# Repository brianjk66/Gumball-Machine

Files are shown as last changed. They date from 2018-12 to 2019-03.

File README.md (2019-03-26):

# Gumball Drink Machine
By Brian Kaplan & Adam Elghor

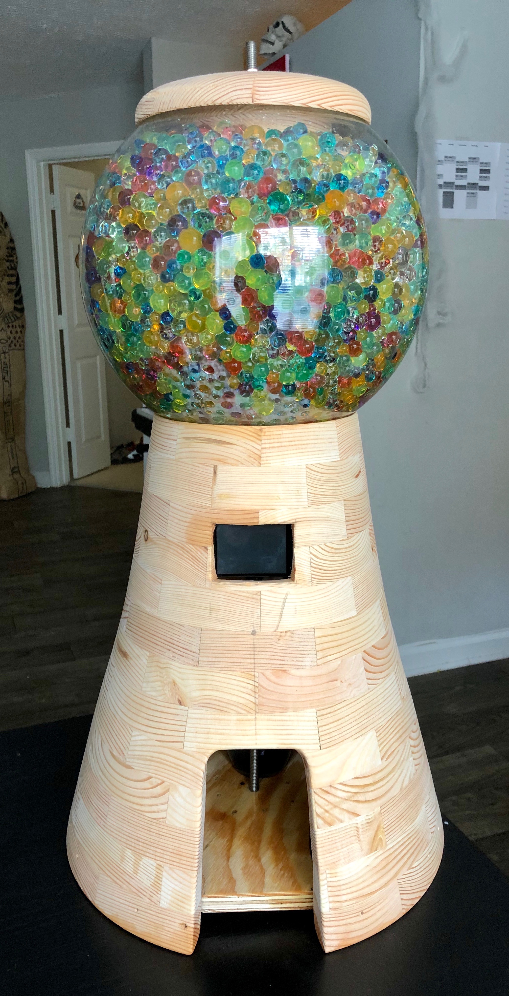
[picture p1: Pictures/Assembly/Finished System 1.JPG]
Finished System


[Project Demo](https://youtu.be/TyXLxnWFjBc)

## Project Idea
The idea of this project was to create an automated drink dispensing system centered around the mbed platform.  This project is intended to be an interactive system that mixes and dispenses internally stored drinks.  We wanted the system to resemble a gumball machine to give it a nice aesthetic and charm.

We decided to make the system gravity-fed for the sake of simplicity with the drinks being stored in a sphere at the top.  The drinks would then be dispensed via solenoid control valves into a cup at the base of the system.  The user interface to the system would be a [TFT LCD touchscreen](https://www.adafruit.com/product/2090) that a user can use to select the drink of their choice.

We also considered the use of [peristaltic pumps](https://www.adafruit.com/product/1150) for better liquid dispensing, a [liquid flow meter](https://www.adafruit.com/product/828) for better liquid measurement, and a [rotary encoder](https://www.adafruit.com/product/377) as an alternate user interface.  However, peristaltic pumps are costly (~$25 each), the flow meter was incredibly bulky and could not fit within the system, and the rotary encoder made for a confusing hybrid UI so we removed it as well.

## Hardware Setup

### Mechanical Components
The mechanical system consists of the following components:
- Handmade wooden body and lid
- 1ft Acrylic Sphere
- Assorted Color Water Beads
- 3ft Threaded Steel Dowel
- 2x Hex Nuts
- 2x Washers
- 4x Condiment Bottles
- 4x 12V Solenoid Valves (food-safe)
- Assorted Push-Fit Connecters and Fittings
- 10ft, 1/4" OD Polyethylene Tubing (food-safe)

### Electrical Components
The electrical system consists of the following components:
- Custom Printed Circuit Board:
  - mbed Microcontroller
  - 5V Linear Voltage Regulator
  - 3.3uF Ceramic Capacitor
  - 1.0uF Ceramic Capacitor
  - 4x 100 Ohm 1/4W Resistors
  - 4x 4.7k Ohm 1/4W Resistors
  - 4x 1N4001 Diodes
  - 4x N-Channel MOSFETs
  - Assorted 0.1" Male Headers
- 2.8in TFT LCD
- Flow Meter (Removed in final design)
- Rotary Encoder (Removed in final design)
- 12V, 2A Power Supply
- Barrel Jack
- Rocker Switch

## Code Setup
This system relies on using Adafruit's TFT LCD touchscreen on the mbed.  However, all of Adafruit's accompanying libraries and software support are made exclusively for Arduino (or Arduino-compatible) products.  As a result, the first major step in the software development of this project was porting the necessary Arduino libraries to the mbed.  The first library that we ported to mbed was [Adafruit's GFX Library](https://github.com/adafruit/Adafruit-GFX-Library) to provide us with a familiar graphics API.  The second library we ported was [Adafruit's ILI9341 Library](https://github.com/adafruit/Adafruit_ILI9341) for interfacing with the LCD.  The third library we ported was [Adafruit's FT6206 Library](https://github.com/adafruit/Adafruit_FT6206_Library) for interfacing with the FT6206 capacitive touch controller on the touchscreen.

Next, we wrote several test programs for testing the functionality of our hardware.  We wrote (and also used some existing) test programs for both the Arduino (before porting the libraries to mbed) and the mbed.  The Arduino test programs included a rotary encoder test, a flow meter test, and a couple LCD tests.  The mbed test programs included a flow sensor test and several LCD tests.

The final program that runs on the system is fairly straightforward.  It features 4 digital outputs for controlling each solenoid valve via a MOSFET.  There is also a touch controller and an LCD object for touchscreen I/O.  Finally a 2D array in program memory stores the hardcoded recipes for each drink.  The rows of the array correspond to recipes and the columns correspond to the proportion of each mixer in the drink.

The main loop body initializes all the peripherals as needed and sets up an interrupt routine for when a user touches the display.  If the user has selected an on-screen button corresponding to a drink, then the system dispenses the drink according to its recipe.  The dispensing routine starts a timer and opens the appropriate valves for durations that are directly proportional to the ratios provided in the recipe. The scaling factor (called TIME_SCALAR) must be calibrated based on the flow of drinks through the system

## Instructions

### Woodwork
The wooden body of the system was made by cutting several carefully measured trapezoids out of 8ft 2x4s and arranging them into 13 octagonal rings of decreasing size.  The rings were then glued together and stacked to form a conical structure.  This was then fastened to a lathe and turned down to the final shape of the system.  Cutouts were then made for the touchscreen and the cup hole.  The lid of the system was also turned on a lathe as well.

### The Sphere
The acrylic sphere had five holes drilled in it (one for structural support and 4 for tubing) and situated on top of the system.  The condiment bottles had holes drilled in their bases and had tubing fed in through the bottom and sealed with a combination of FDA-approved silicone sealant and hot glue.  The condiment bottles were placed in the sphere with the tubing passing through the previously mentioned holes and the lid was placed on top.  The threaded steel rod was cut to about 30" and fed through the lid, sphere, and bottom faceplate to serve as a central support column for the system, secured by a nut and washer on either side.

### Plumbing
The tubing assembly of the system consisted of the 4 solenoids connecting to the condiment bottles on one side.  On the other side, the solenoids connected to a set of Y-connectors to merge the 4 tubes into one for the output nozzle.  This tubing assembly was secured to the inside of the wooden body using hot glue.

### Electrical
The electrical system consisted primarily of a PCB.  The PCB took a 12V input for power and an onboard linear regulator to step the power down to 5V for the LCD and flow meter (which was later removed).  The PCB featured 4 driver sub-circuits to allow the mbed to open and close the solenoid valves (which used 12V power) via a DigitalOut pin.  The driver sub-circuits consisted of an N-channel MOSFET, a gate drive resistor, a gate pulldown resistor, and a fly-back diode.  The PCB connected touchscreen, the driver sub-circuits, the rotary encoder (removed), and the flow meter (removed) all to the appropriate mbed ports.  The PCB and touchscreen were mounted inside the body of the system using hot glue.

## Acknowledgements
We'd like to thank the PI's of the Invention Studio for all their help on this project and for providing us access to their incredible facilities for wood-working, metal-working, soldering, and PCB manufacturing.  We'd especially like to thank Morgan Cook, the Invention Studio's Director of Operations, for his continued help and support.

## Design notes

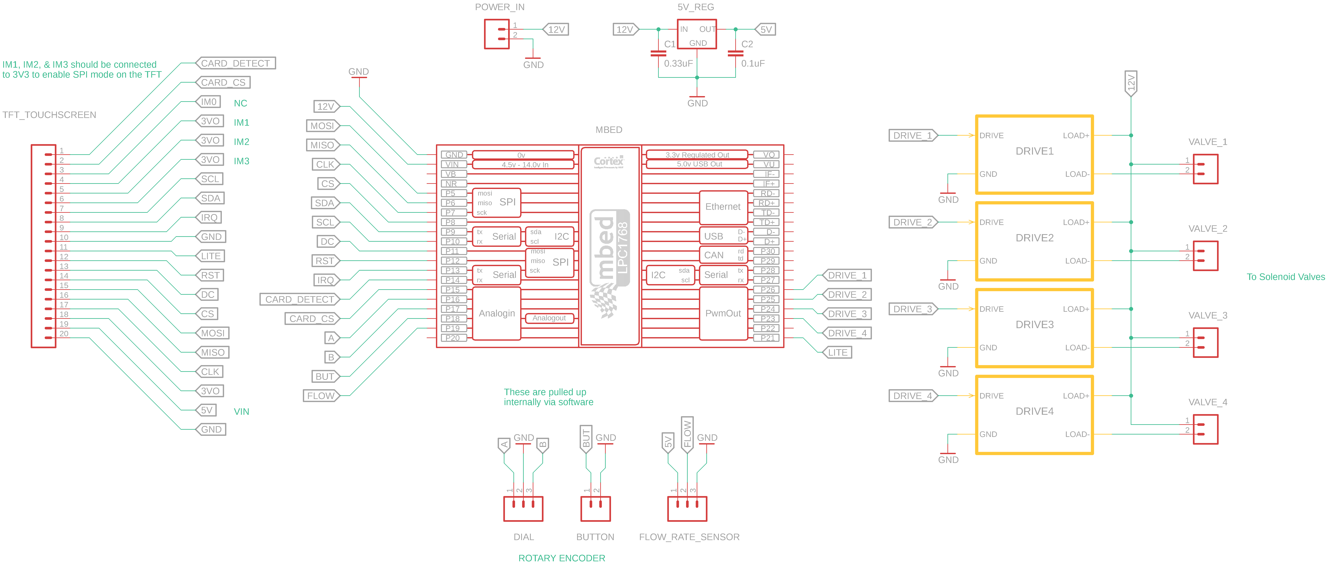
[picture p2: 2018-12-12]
Pictures/Electrical System/PCB Schematic.png

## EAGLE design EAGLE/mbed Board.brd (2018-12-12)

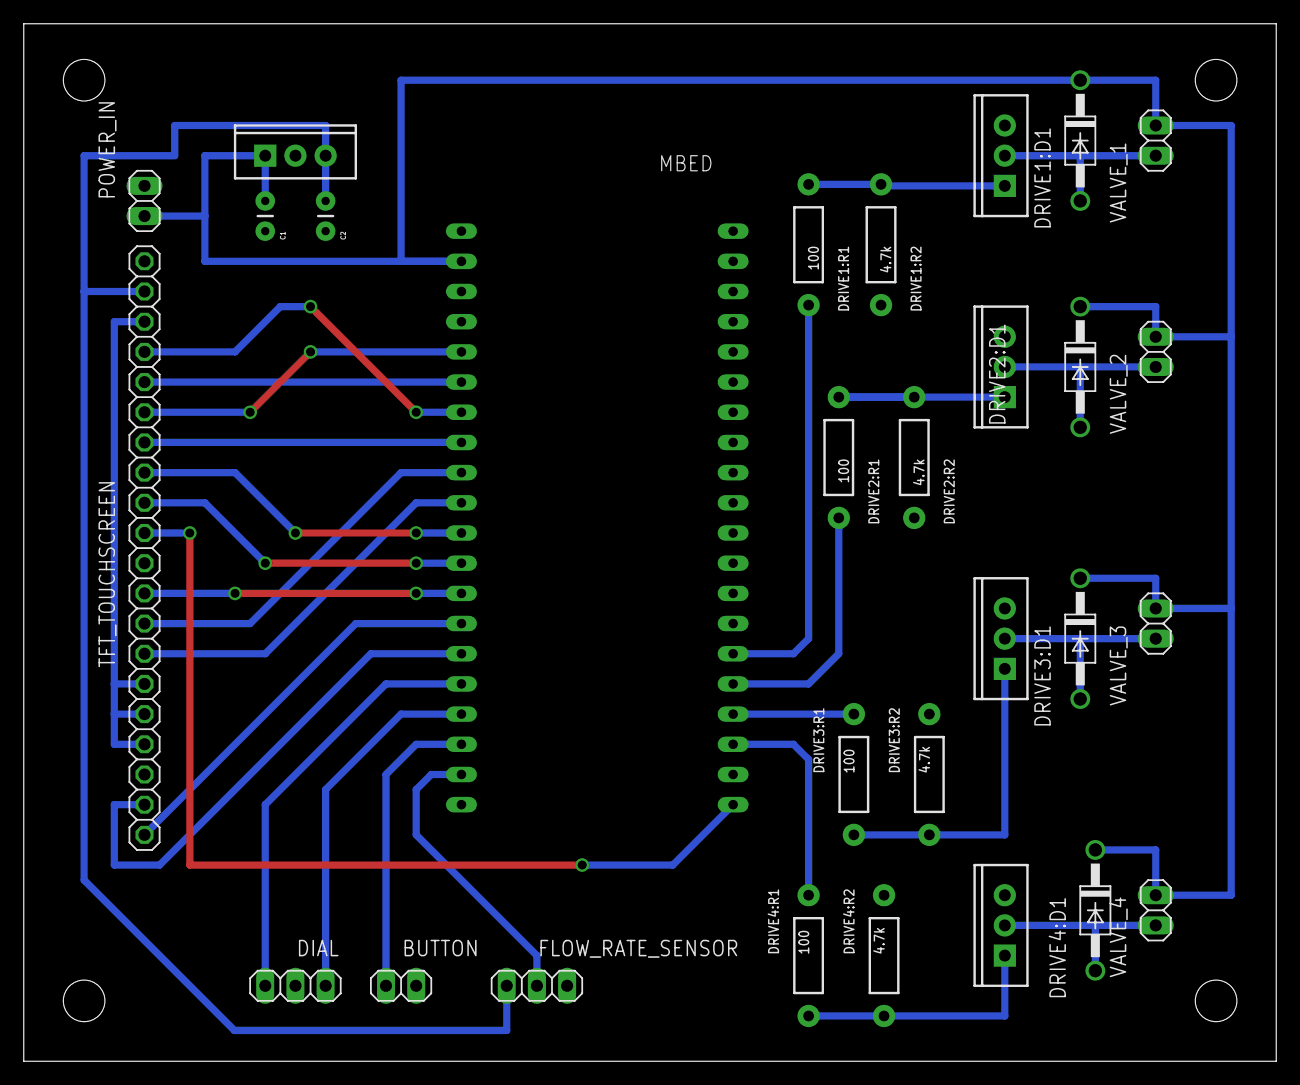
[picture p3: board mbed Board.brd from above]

Board: 2 copper layers, 105.4 x 87.3 mm, 29 parts (0 on the bottom side), 32 nets.

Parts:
5V_REG: TO-220-SINK
BUTTON: 1X02
C1: 0.33uF; CAP-PTH-SMALL
C2: 0.1uF; CAP-PTH-SMALL
DIAL: 1X03
DRIVE1:D1, DRIVE2:D1, DRIVE3:D1, DRIVE4:D1: DO-41
DRIVE1:NFET, DRIVE2:NFET, DRIVE3:NFET, DRIVE4:NFET: N-CHANNEL_MOSFETGENERIC; TO-220-SINK
DRIVE1:R1, DRIVE2:R1, DRIVE3:R1, DRIVE4:R1: 100; AXIAL-0.4
DRIVE1:R2, DRIVE2:R2, DRIVE3:R2, DRIVE4:R2: 4.7k; AXIAL-0.4
FLOW_RATE_SENSOR: 1X03
MBED: MBED_NXP_LPC1768; MBED-KIT
POWER_IN: 1X02
TFT_TOUCHSCREEN: 1X20
VALVE_1, VALVE_2, VALVE_3, VALVE_4: 1X02

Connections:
3VO: TFT_TOUCHSCREEN.4, TFT_TOUCHSCREEN.5, TFT_TOUCHSCREEN.6, TFT_TOUCHSCREEN.18
5V: 5V_REG.3, C2.1, FLOW_RATE_SENSOR.1, TFT_TOUCHSCREEN.19
12V: 5V_REG.1, C1.1, DRIVE1:D1.C, DRIVE2:D1.C, DRIVE3:D1.C, DRIVE4:D1.C, MBED.VIN, POWER_IN.1, VALVE_1.1, VALVE_2.1, VALVE_3.1, VALVE_4.1
A: DIAL.1, MBED.P$16
B: DIAL.3, MBED.P$17
BUT: BUTTON.1, MBED.P$18
CARD_CS: MBED.P$15, TFT_TOUCHSCREEN.2
CARD_DETECT: MBED.P$14, TFT_TOUCHSCREEN.1
CLK: MBED.P$7, TFT_TOUCHSCREEN.17
CS: MBED.P$8, TFT_TOUCHSCREEN.14
DC: MBED.P$11, TFT_TOUCHSCREEN.13
DRIVE1:N$4: DRIVE1:NFET.1, DRIVE1:R1.P$1, DRIVE1:R2.P$1
DRIVE2:N$4: DRIVE2:NFET.1, DRIVE2:R1.P$1, DRIVE2:R2.P$1
DRIVE3:N$4: DRIVE3:NFET.1, DRIVE3:R1.P$1, DRIVE3:R2.P$1
DRIVE4:N$4: DRIVE4:NFET.1, DRIVE4:R1.P$1, DRIVE4:R2.P$1
DRIVE_1: DRIVE1:R1.P$2, MBED.P$26
DRIVE_2: DRIVE2:R1.P$2, MBED.P$25
DRIVE_3: DRIVE3:R1.P$2, MBED.P$24
DRIVE_4: DRIVE4:R1.P$2, MBED.P$23
FLOW: FLOW_RATE_SENSOR.2, MBED.P$19
GND: 5V_REG.2, BUTTON.2, C1.2, C2.2, DIAL.2, DRIVE1:NFET.3, DRIVE1:R2.P$2, DRIVE2:NFET.3, DRIVE2:R2.P$2, DRIVE3:NFET.3, DRIVE3:R2.P$2, DRIVE4:NFET.3, DRIVE4:R2.P$2, FLOW_RATE_SENSOR.3, MBED.GND, POWER_IN.2, TFT_TOUCHSCREEN.10, TFT_TOUCHSCREEN.20
IRQ: MBED.P$13, TFT_TOUCHSCREEN.9
LITE: MBED.P$21, TFT_TOUCHSCREEN.11
MISO: MBED.P$6, TFT_TOUCHSCREEN.16
MOSI: MBED.P$5, TFT_TOUCHSCREEN.15
unnamed: DRIVE2:D1.A, DRIVE2:NFET.2, VALVE_2.2
unnamed: DRIVE3:D1.A, DRIVE3:NFET.2, VALVE_3.2
unnamed: DRIVE4:D1.A, DRIVE4:NFET.2, VALVE_4.2
unnamed: DRIVE1:D1.A, DRIVE1:NFET.2, VALVE_1.2
RST: MBED.P$12, TFT_TOUCHSCREEN.12
SCL: MBED.P$10, TFT_TOUCHSCREEN.7
SDA: MBED.P$9, TFT_TOUCHSCREEN.8

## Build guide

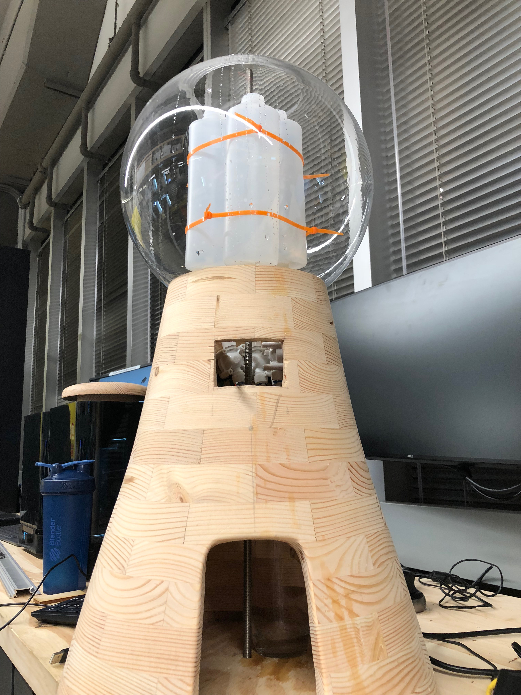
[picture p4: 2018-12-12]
Pictures/Assembly/Condiment Bottles with Zip Ties.jpeg

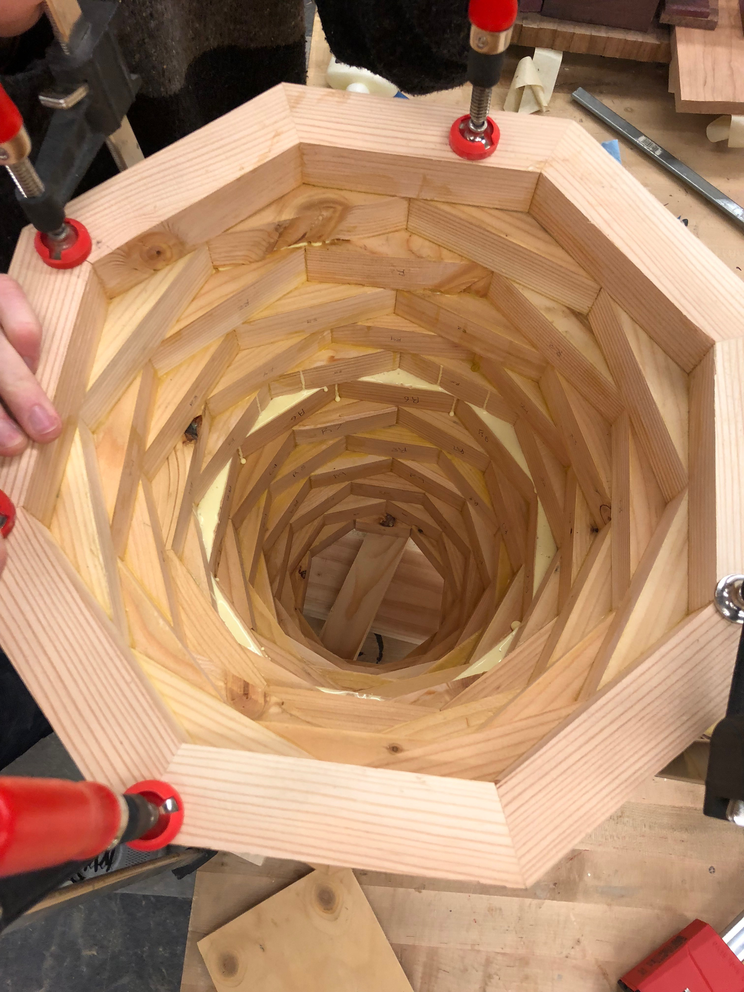
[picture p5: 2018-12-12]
Pictures/Wood Work/Inside Ring Assembly 1.JPG

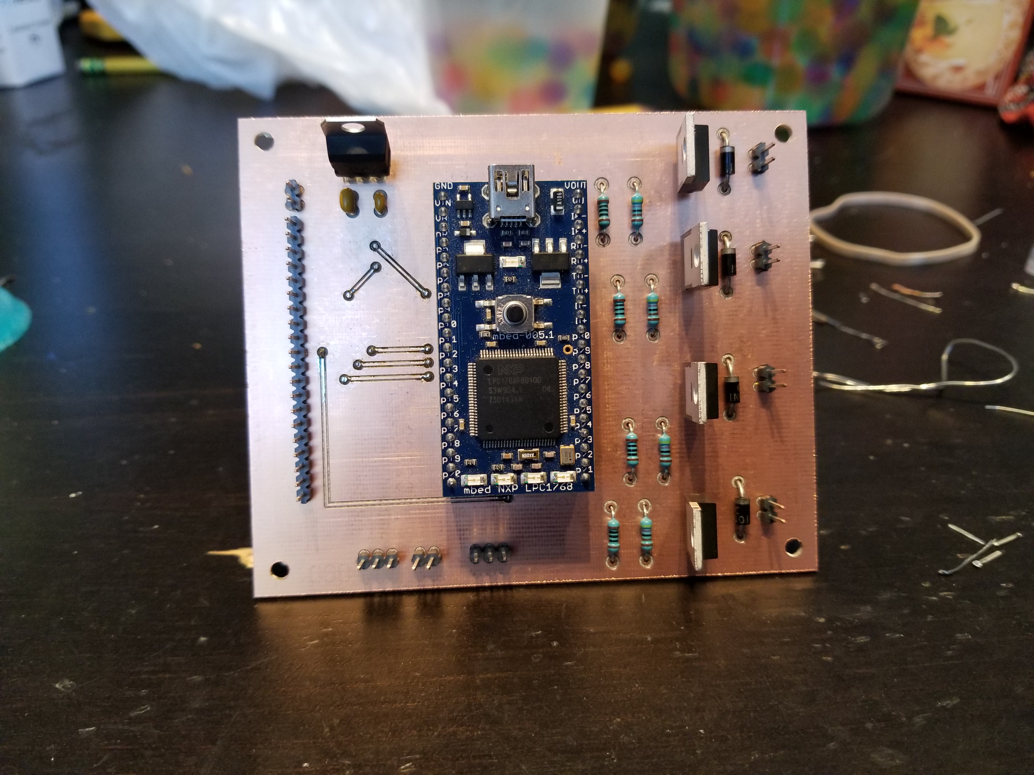
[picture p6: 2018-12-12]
Pictures/Electrical System/Soldered PCB 3.jpg

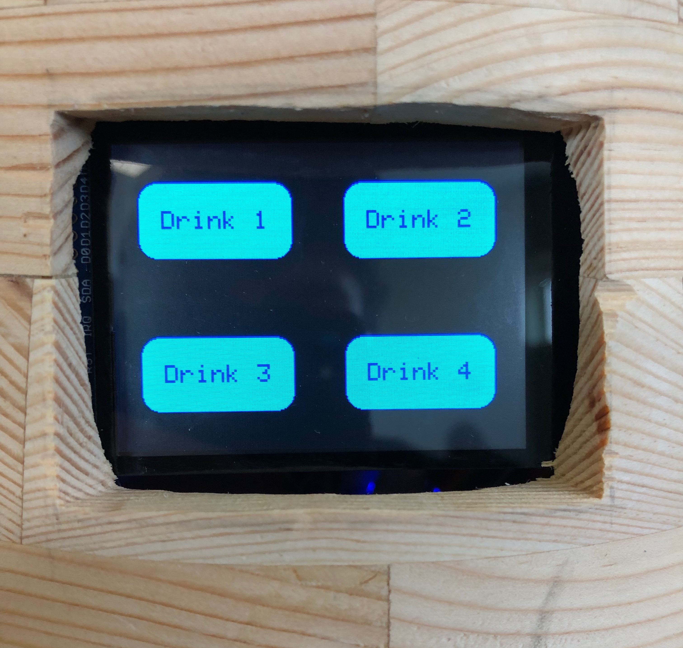
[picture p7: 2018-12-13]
Pictures/Assembly/Touchscreen Display.JPG

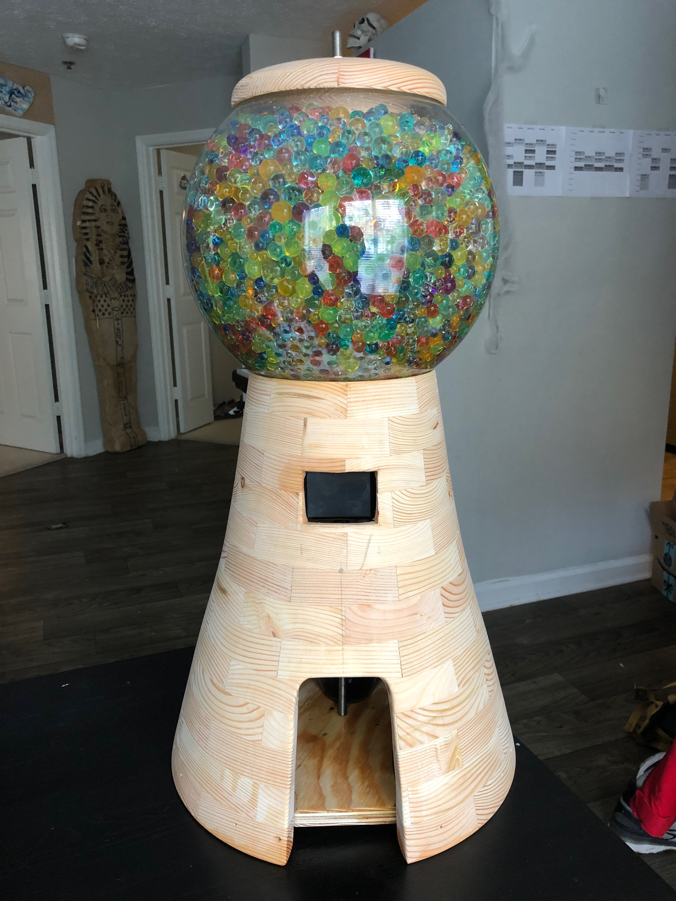
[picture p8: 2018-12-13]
Pictures/Assembly/Finished System 2.JPG

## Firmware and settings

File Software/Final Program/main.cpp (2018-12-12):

#include "mbed.h"
#include "QEI.h"
#include <Adafruit_GFX.h>
#include <Adafruit_ILI9341.h>
#include <Adafruit_FT6206.h>

// Graphics Constants
#define HEIGHT            (240)
#define WIDTH             (320)
#define X_CENTER          (WIDTH / 2)
#define Y_CENTER          (HEIGHT / 2)
#define NUM_BUTTONS       (4)
#define BUTTON_HEIGHT     (60)
#define BUTTON_WIDTH      (120)
#define BUTTON_COLOR      (ILI9341_CYAN)
#define BUTTON_TEXT_COLOR (ILI9341_BLUE)

// Touchscreen Pins
#define TFT_MOSI         p5     // LCD Controller MOSI
#define TFT_MISO         p6     // LCD Controller MISO
#define TFT_SCLK         p7     // LCD Controller SCLK
#define TFT_CS           p8     // LCD Controller Chip Select
#define TFT_DC           p11    // LCD Controller Data/Command
#define TFT_RST          p12    // LCD Reset
#define TFT_SDA          p9     // Touch Controller SDA
#define TFT_SCL          p10    // Touch Controller SCL
#define TFT_INT          p13    // Touch Controller Interrupt Line
#define TFT_CARD_DETECT  p14    // SD Card Detect Pin
#define TFT_CARD_CS      p15    // SD Card Chip Select
#define TFT_BACKLITE     p21    // Touch Screen Backlight

// Solenoids
#define VALVE_1          p26    // MOSFET drive pin for solenoid 1
#define VALVE_2          p25    // MOSFET drive pin for solenoid 2
#define VALVE_3          p24    // MOSFET drive pin for solenoid 3
#define VALVE_4          p23    // MOSFET drive pin for solenoid 4

// Must be calibrated based on flow of drinks
#define TIME_SCALAR      10     // Scalar for timing of drink dispensing


void up();
void down();

// Solenoid Valve Conrols
DigitalOut valve1(VALVE_1);
DigitalOut valve2(VALVE_2);
DigitalOut valve3(VALVE_3);
DigitalOut valve4(VALVE_4);

// USB serial communication
Serial pc(USBTX, USBRX);

// 2.8" TFT Touchscreen with ILI9341 (SPI communication)
SPI spi(TFT_MOSI, TFT_MISO, TFT_SCLK);
Adafruit_ILI9341 tft(&spi, TFT_CS, TFT_DC, TFT_RST);

// FT6206 Touch Controller (I2C communication)
I2C i2c(TFT_SDA, TFT_SCL);
InterruptIn interrupt(TFT_INT);
Adafruit_FT6206 ctp(&i2c);

// Data structures for managing buttons
Adafruit_GFX_Button buttons[NUM_BUTTONS];

// Global Variables
int scrollOffset = 0;
bool newOffset = false;
char buttonName[] = "Drink X";
int index;

Timer timer;

const int recipes[4][4] {
    // Drink 1 (Even mix of everything)
    { 1, 1, 1, 1},
    // Drink 2 (2:1 Ratio of Mixer 1 to Mixer 2)  
    { 2, 1, 0, 0},
    // Drink 3 (1:1 Ratio of Mixer 3 to Mixer 4)
    { 0, 0, 1, 1},
    // Drink 4 (Just Drink 4)
    { 0, 0, 0, 1}
};

// Function Declarations
void makeDrink(int);
void justPressed(int);
void touched();
void drawButtons();


void makeDrink(int num) {
    bool stop = false;
    float seconds;
    
    // Disable interrupts while dispensing
    interrupt.fall(NULL);
    
    // Start timer
    timer.start();
    
    // Turn on valves
    if (recipes[num][0])
        valve1 = 1;
    if (recipes[num][1])
        valve2 = 1;
    if (recipes[num][2])
        valve3 = 1;
    if (recipes[num][3])
        valve4 = 1;
    
    // Wait until drink is dispensed
    while (!stop) {
        // Sample the timer
        seconds = timer.read();
        
        stop = true;
        
        // Check each drink
        for (int i = 0; i < 4; i++) {
            // If the timer has expired for a mixer, shut off its valve
            if (seconds >= (TIME_SCALAR * recipes[num][i])) {
                switch (i) {
                    case 0:
                        valve1 = 0;
                        break;
                    case 1:
                        valve2 = 0;
                        break;
                    case 2:   
                        valve3 = 0;
                        break;
                    case 3: 
                        valve4 = 0;
                        break;
                }
            } else {
                // Otherwise, don't stop
                stop = false;
            }
        }
    }
    
    // Stop and reset timer
    timer.stop();
    timer.reset();
    
    // Re-draw buttons
    drawButtons();
    
    // Re-attach ISR to interrupt pin
    interrupt.fall(&touched);
}

// Action to take when button at specified index is pressed
void justPressed(int index) {
    // Clear Screen
    tft.fillScreen(ILI9341_BLACK);
    
    // Write text in white
    tft.setCursor(0, Y_CENTER);
    tft.setTextColor(ILI9341_WHITE);
    tft.setTextSize(2);
    tft.printf("    Dispensing Drink %d! ", index+1);
    
    // Make drink
    makeDrink(index);
}

void touched() {
    // Retrieve a point  
    TS_Point p = ctp.getPoint();
    
    // flip it around to match the screen.
//    p.x = HEIGHT - p.x;
    p.y = WIDTH - p.y;
    
    // Check if buttons were pressed
    for (int i = 0; i < NUM_BUTTONS; i++)
        // Swap X & Y because of screen rotation
        buttons[i].press(buttons[i].contains(p.y, p.x));
    
    for (int i = 0; i < NUM_BUTTONS; i++) {
        if (buttons[i].justPressed()) {
            justPressed(i);
            break;
        }
    }
}

void drawButtons() {
     // Clear screen
     tft.fillScreen(ILI9341_BLACK);

    // Initialize and draw each button    
    for (int i = 0; i < NUM_BUTTONS/2; i++) {
        for (int j = 0; j < NUM_BUTTONS/2; j++) {      
            buttonName[6] = '1' + 2*i + j;
            buttons[2*i + j].initButton(&tft, X_CENTER/2+(j*X_CENTER), Y_CENTER/2+(i*Y_CENTER), BUTTON_WIDTH, BUTTON_HEIGHT, BUTTON_TEXT_COLOR, BUTTON_COLOR, BUTTON_TEXT_COLOR, buttonName, 2);
            buttons[2*i + j].drawButton();
        }
    }
}

int main() {
    printf("Cap Touch Button!\n\r");
    
    tft.begin();
    
    // Orient screen horizontally
    tft.setRotation(1);
    
    if (! ctp.begin(40)) {  // pass in 'sensitivity' coefficient
        printf("Couldn't start FT6206 touchscreen controller\n\r");
        while (1);
    }
    
    printf("Capacitive touchscreen started\n\r");
        
    // Draw buttons
    drawButtons();
    
    // Attach ISR to interrupt pin
    interrupt.fall(&touched);
  
    // Spin and wait for interrupts
    while (1);
}

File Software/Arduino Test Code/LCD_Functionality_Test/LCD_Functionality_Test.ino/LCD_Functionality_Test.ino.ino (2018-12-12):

/***************************************************
  This is an example sketch for the Adafruit 1.8" SPI display.
  This library works with the Adafruit 1.8" TFT Breakout w/SD card
  ----> http://www.adafruit.com/products/358
  as well as Adafruit raw 1.8" TFT display
  ----> http://www.adafruit.com/products/618
 
  Check out the links above for our tutorials and wiring diagrams
  These displays use SPI to communicate, 4 or 5 pins are required to
  interface (RST is optional)
  Adafruit invests time and resources providing this open source code,
  please support Adafruit and open-source hardware by purchasing
  products from Adafruit!

  Written by Limor Fried/Ladyada for Adafruit Industries.
  MIT license, all text above must be included in any redistribution
 ****************************************************/

// This Teensy3 native optimized version requires specific pins
//
#define sclk 13  // SCLK can also use pin 14
#define mosi 11  // MOSI can also use pin 7
#define cs   10  // CS & DC can use pins 2, 6, 9, 10, 15, 20, 21, 22, 23
#define dc   14  //  but certain pairs must NOT be used: 2+10, 6+9, 20+23, 21+22
#define rst  15  // RST can use any pin
#define sdcs 9   // CS for SD card, can use any pin

#include <Adafruit_GFX.h>    // Core graphics library
#include <Adafruit_ST7735.h> // Hardware-specific library
#include <SPI.h>

#if defined(__SAM3X8E__)
    #undef __FlashStringHelper::F(string_literal)
    #define F(string_literal) string_literal
#endif

// Option 1: use any pins but a little slower
Adafruit_ST7735 tft = Adafruit_ST7735(cs, dc, mosi, sclk, rst);

// Option 2: must use the hardware SPI pins
// (for UNO thats sclk = 13 and sid = 11) and pin 10 must be
// an output. This is much faster - also required if you want
// to use the microSD card (see the image drawing example)
//Adafruit_ST7735 tft = Adafruit_ST7735(cs, dc, rst);
float p = 3.1415926;

 
#define Neutral 0
#define Press 1
#define Up 2
#define Down 3
#define Right 4
#define Left 5
 
// Check the joystick position
int CheckJoystick()
{
  int joystickState = analogRead(3);
  
  if (joystickState < 50) return Left;
  if (joystickState < 150) return Down;
  if (joystickState < 250) return Press;
  if (joystickState < 500) return Right;
  if (joystickState < 650) return Up;
  return Neutral;
}


void setup(void) {
  pinMode(sdcs, INPUT_PULLUP);  // don't touch the SD card
  Serial.begin(9600);
  Serial.print("hello!");

  // Our supplier changed the 1.8" display slightly after Jan 10, 2012
  // so that the alignment of the TFT had to be shifted by a few pixels
  // this just means the init code is slightly different. Check the
  // color of the tab to see which init code to try. If the display is
  // cut off or has extra 'random' pixels on the top & left, try the
  // other option!
  // If you are seeing red and green color inversion, use Black Tab

  // If your TFT's plastic wrap has a Black Tab, use the following:
//  tft.initR(INITR_BLACKTAB);   // initialize a ST7735S chip, black tab
  // If your TFT's plastic wrap has a Red Tab, use the following:
  //tft.initR(INITR_REDTAB);   // initialize a ST7735R chip, red tab
  // If your TFT's plastic wrap has a Green Tab, use the following:
  tft.initR(INITR_GREENTAB); // initialize a ST7735R chip, green tab

  Serial.println("init");

  uint16_t time = millis();
  tft.fillScreen(ST7735_BLACK);
  time = millis() - time;

  Serial.println(time, DEC);
  delay(500);

  // large block of text
  tft.fillScreen(ST7735_BLACK);
  testdrawtext("Lorem ipsum dolor sit amet, consectetur adipiscing elit. Curabitur adipiscing ante sed nibh tincidunt feugiat. Maecenas enim massa, fringilla sed malesuada et, malesuada sit amet turpis. Sed porttitor neque ut ante pretium vitae malesuada nunc bibendum. Nullam aliquet ultrices massa eu hendrerit. Ut sed nisi lorem. In vestibulum purus a tortor imperdiet posuere. ", ST7735_WHITE);
  delay(1000);

  // tft print function!
  tftPrintTest();
  delay(4000);

  // a single pixel
  tft.drawPixel(tft.width()/2, tft.height()/2, ST7735_GREEN);
  delay(500);

  // line draw test
  testlines(ST7735_YELLOW);
  delay(500);

  // optimized lines
  testfastlines(ST7735_RED, ST7735_BLUE);
  delay(500);

  testdrawrects(ST7735_GREEN);
  delay(500);

  testfillrects(ST7735_YELLOW, ST7735_MAGENTA);
  delay(500);

  tft.fillScreen(ST7735_BLACK);
  testfillcircles(10, ST7735_BLUE);
  testdrawcircles(10, ST7735_WHITE);
  delay(500);

  testroundrects();
  delay(500);

  testtriangles();
  delay(500);

  mediabuttons();
  delay(500);

  Serial.println("done");
  delay(1000);
}

void loop() {
  tft.invertDisplay(true);
  delay(500);
  tft.invertDisplay(false);
  delay(500);
  int joy = CheckJoystick();
  switch (joy)
  {
    case Left:
      Serial.println("Left");
      break;
    case Right:
      Serial.println("Right");
      break;
    case Up:
      Serial.println("Up");
      break;
    case Down:
      Serial.println("Down");
      break;
    case Press:
      Serial.println("Press");
      break;
  }
}

void testlines(uint16_t color) {
  tft.fillScreen(ST7735_BLACK);
  for (int16_t x=0; x < tft.width(); x+=6) {
    tft.drawLine(0, 0, x, tft.height()-1, color);
  }
  for (int16_t y=0; y < tft.height(); y+=6) {
    tft.drawLine(0, 0, tft.width()-1, y, color);
  }

  tft.fillScreen(ST7735_BLACK);
  for (int16_t x=0; x < tft.width(); x+=6) {
    tft.drawLine(tft.width()-1, 0, x, tft.height()-1, color);
  }
  for (int16_t y=0; y < tft.height(); y+=6) {
    tft.drawLine(tft.width()-1, 0, 0, y, color);
  }

  tft.fillScreen(ST7735_BLACK);
  for (int16_t x=0; x < tft.width(); x+=6) {
    tft.drawLine(0, tft.height()-1, x, 0, color);
  }
  for (int16_t y=0; y < tft.height(); y+=6) {
    tft.drawLine(0, tft.height()-1, tft.width()-1, y, color);
  }

  tft.fillScreen(ST7735_BLACK);
  for (int16_t x=0; x < tft.width(); x+=6) {
    tft.drawLine(tft.width()-1, tft.height()-1, x, 0, color);
  }
  for (int16_t y=0; y < tft.height(); y+=6) {
    tft.drawLine(tft.width()-1, tft.height()-1, 0, y, color);
  }
}

void testdrawtext(const char *text, uint16_t color) {
  tft.setCursor(0, 0);
  tft.setTextColor(color);
  tft.setTextWrap(true);
  tft.print(text);
}

void testfastlines(uint16_t color1, uint16_t color2) {
  tft.fillScreen(ST7735_BLACK);
  for (int16_t y=0; y < tft.height(); y+=5) {
    tft.drawFastHLine(0, y, tft.width(), color1);
  }
  for (int16_t x=0; x < tft.width(); x+=5) {
    tft.drawFastVLine(x, 0, tft.height(), color2);
  }
}

void testdrawrects(uint16_t color) {
  tft.fillScreen(ST7735_BLACK);
  for (int16_t x=0; x < tft.width(); x+=6) {
    tft.drawRect(tft.width()/2 -x/2, tft.height()/2 -x/2 , x, x, color);
  }
}

void testfillrects(uint16_t color1, uint16_t color2) {
  tft.fillScreen(ST7735_BLACK);
  for (int16_t x=tft.width()-1; x > 6; x-=6) {
    tft.fillRect(tft.width()/2 -x/2, tft.height()/2 -x/2 , x, x, color1);
    tft.drawRect(tft.width()/2 -x/2, tft.height()/2 -x/2 , x, x, color2);
  }
}
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
